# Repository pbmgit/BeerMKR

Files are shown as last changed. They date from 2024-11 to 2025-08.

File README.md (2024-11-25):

# BeerMKR
Extensions to BeerMKR machine to keep brewing if no AWS

History

I've really enjoyed brewing with the BeerMKR and I'm an Engineer (at least that's what my 40 year old degree says).
So I link to tinker and understand how and why things work.  

That applies to the beer I brew, I like to experiment.
And now that applies to the BeerMKR machine.

My BeerMKR tinkering started when I just wasn't cooling as well as I once was.  I started measuring voltages and currents on the Pelteir and decided that the heating and cooling cycles on the Peltier might have caused cracking in the solder joints which caused the resistance to rise and the current flow to fall.  With a Peltier heat transfer is proportional to current flow.
Part of that was based on this article https://www.sameskydevices.com/blog/reliability-considerations-for-peltier-modules
I also researched and changed my vibrator motor since the bushings on the original motor were so far gone that the rotor was hitting the magnets.

When I replaced the Peltier I found that I was cooling better than ever but I had some odd issues with brewing.  That got me to investigating how and when the heaters go turned on.
After that I brewed with my board connected, but clear out of my machine as I tried to figure things out.
It seems that the software on my BeerMKR board just wasn't compatible with my new Peltier.  So I started to figure out how to do the job without the BeerMKR computer.

I mapped out the connectors and ordered some of them.
I gleaned what I could from the BeerMKR board design - what parts do what.

Development

I started thinking about what I could without completely inventing the wheel.  Unrelated to my brewing I had been updating my 3D printer.  The 3D printer has temperature readings and power controls to manage the heated bed and extruder.  I thought I might use that to control the Peltier and heaters on the BeerMKR instead.
I successfully got a code change into the Marlin project that allows the heated bed power circuitry to be used to control a Peltier device (in 3D printing, when you want to cool down you just turn off whichever heater - you don't actively cool)

The BeerMKR board uses an "H-Bridge" consisting of 4 power FET transistors to turn on the Peltier in either direction.  Since the Peltier draws in excess of 8A that takes some care to replicate.
For my first pass I just used a DPDT relay configured as an H-Bridge.
For my Marlin setup I used an Arduino Mega board with a "RAMPS" (RepRap Arduino Mega Pololu Shield) to plug in on top of the Mega.  The RAMPS board has some power electronics for the heaters that we'll use and some sockets for Pololu stepper motor controls that we won't use.

For the first test the Mega was plugged into a laptop and the brewing was controlled through a serial port.  Not exactly automation, but it worked.

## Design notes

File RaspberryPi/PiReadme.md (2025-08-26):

## Current Pi settings

| | |
|:---|:---|
| Raspberry PI Imager | https://downloads.raspberrypi.org/imager/imager_latest.exe  |
| Raspberry Pi OS Lite| https://www.raspberrypi.com/software/operating-systems/ |

```
sudo apt-get update
sudo apt-get install python3-pip

sudo apt-get install python3-serial 

sudo apt install apache2 -y
sudo apt install php -y

sudo apt install python3-usb
```

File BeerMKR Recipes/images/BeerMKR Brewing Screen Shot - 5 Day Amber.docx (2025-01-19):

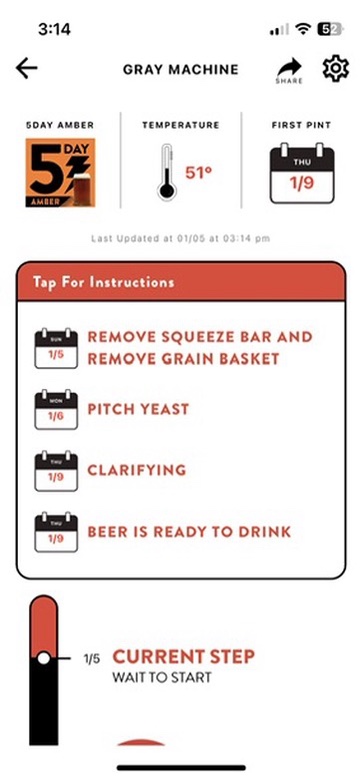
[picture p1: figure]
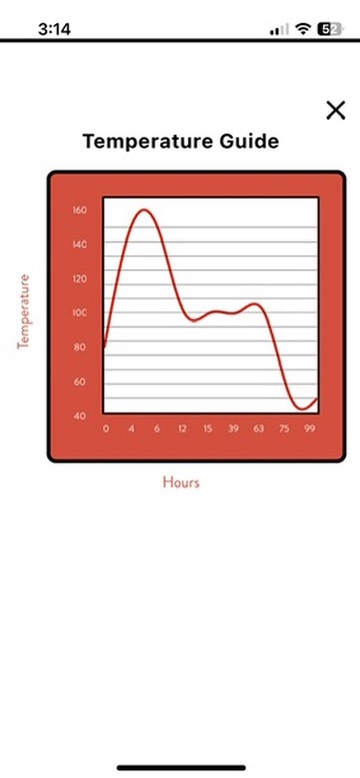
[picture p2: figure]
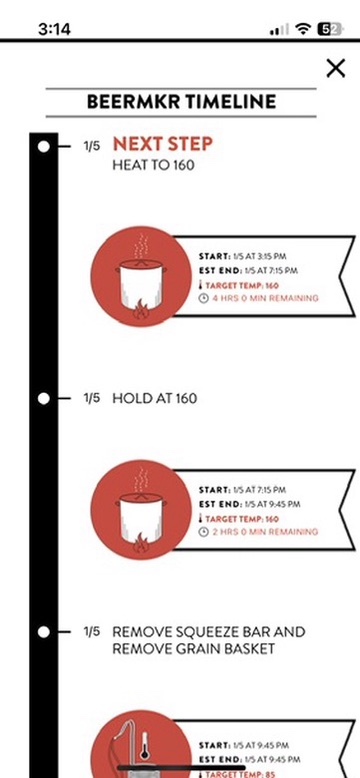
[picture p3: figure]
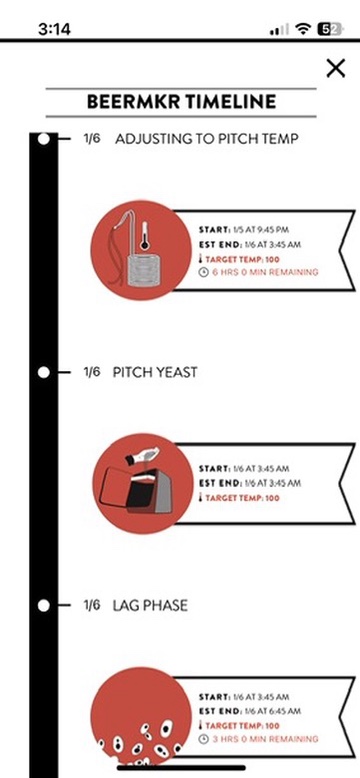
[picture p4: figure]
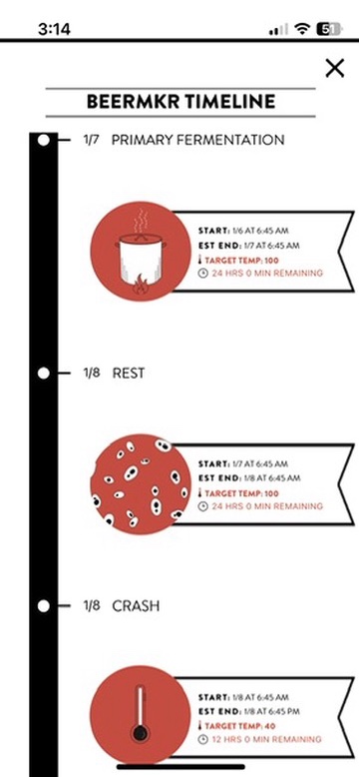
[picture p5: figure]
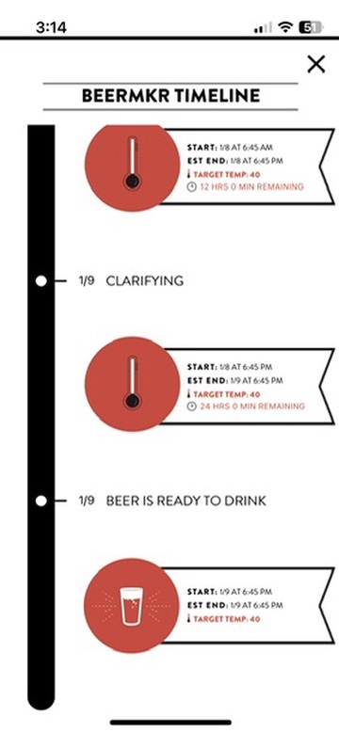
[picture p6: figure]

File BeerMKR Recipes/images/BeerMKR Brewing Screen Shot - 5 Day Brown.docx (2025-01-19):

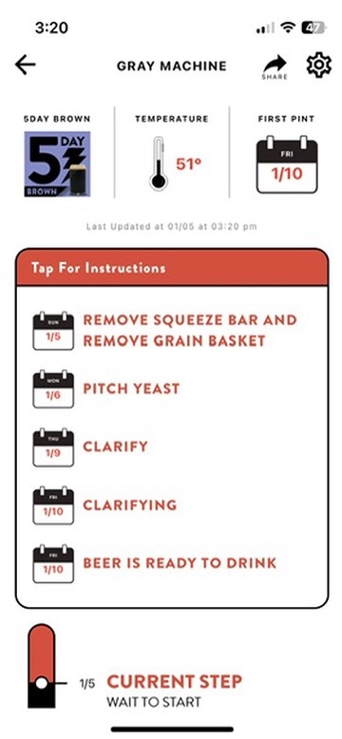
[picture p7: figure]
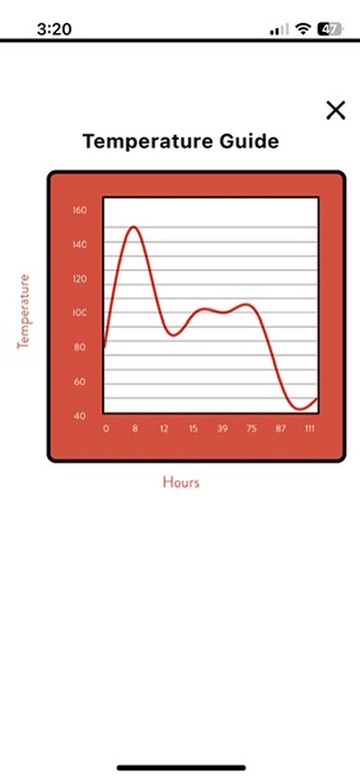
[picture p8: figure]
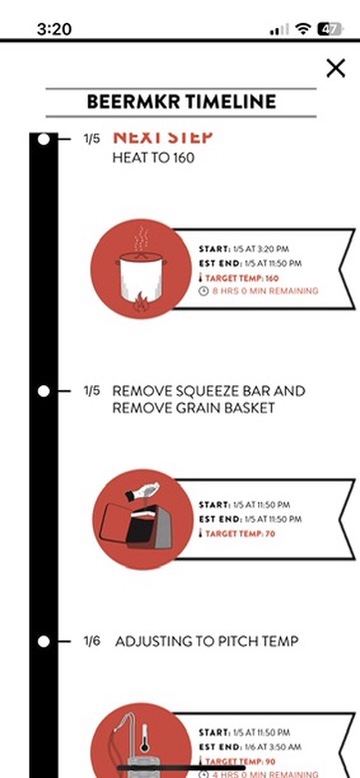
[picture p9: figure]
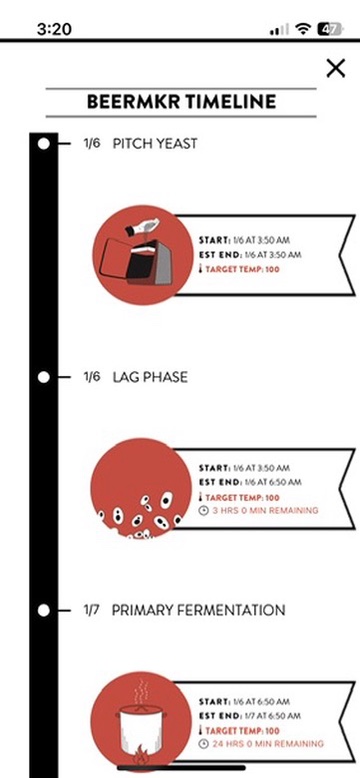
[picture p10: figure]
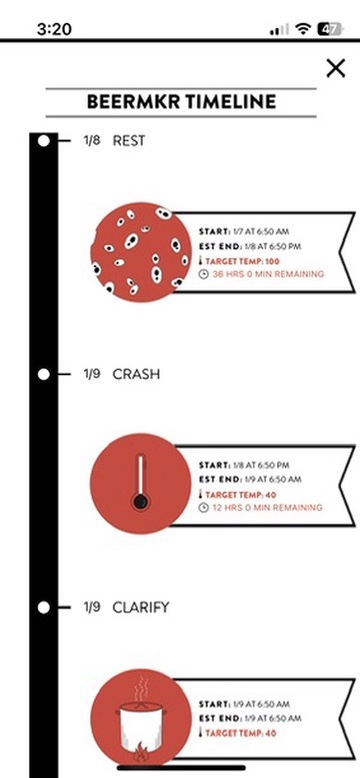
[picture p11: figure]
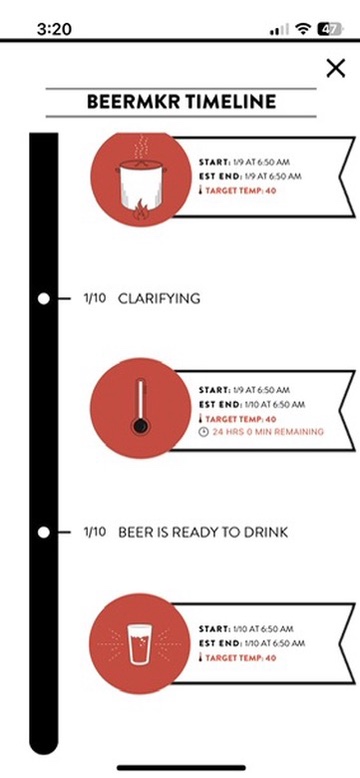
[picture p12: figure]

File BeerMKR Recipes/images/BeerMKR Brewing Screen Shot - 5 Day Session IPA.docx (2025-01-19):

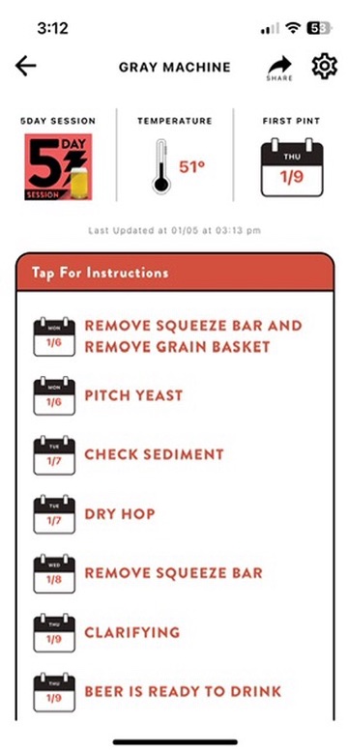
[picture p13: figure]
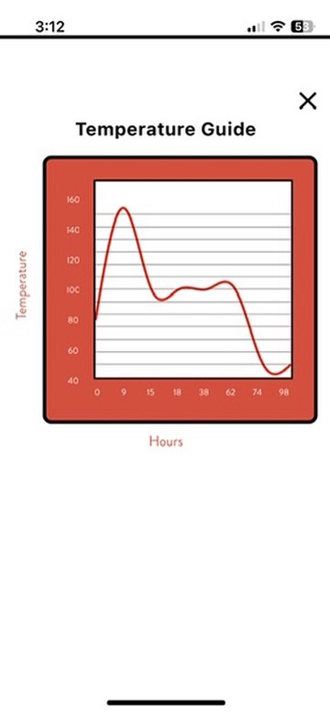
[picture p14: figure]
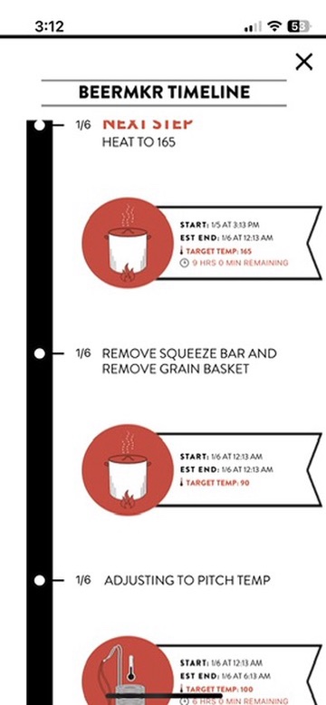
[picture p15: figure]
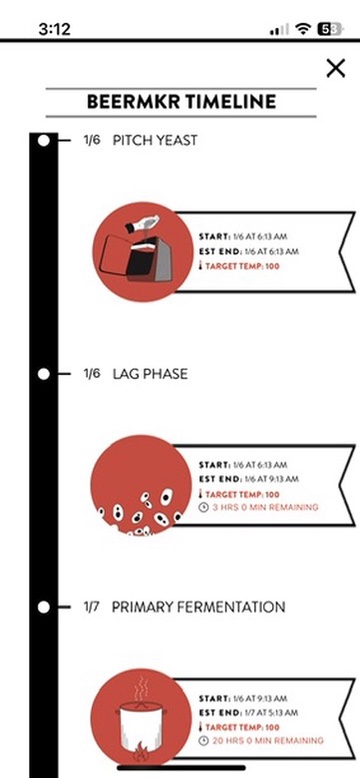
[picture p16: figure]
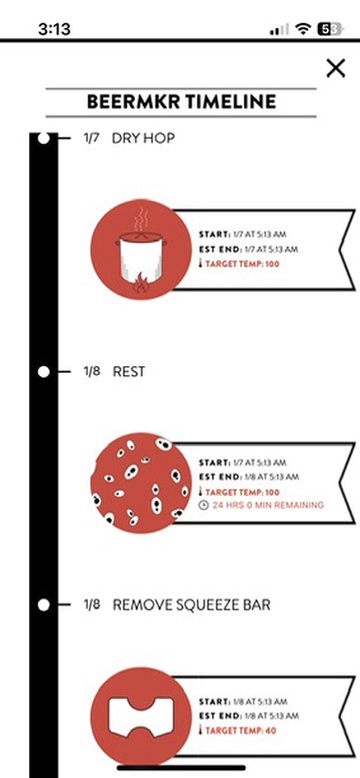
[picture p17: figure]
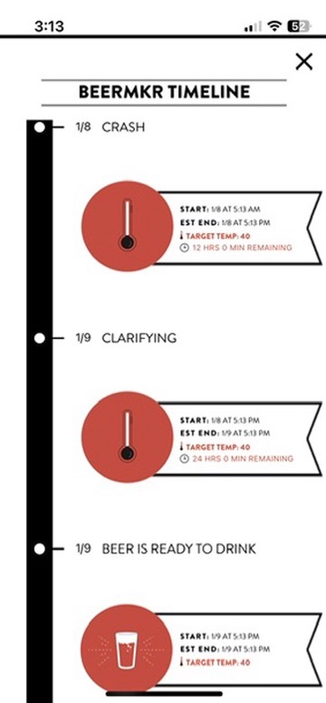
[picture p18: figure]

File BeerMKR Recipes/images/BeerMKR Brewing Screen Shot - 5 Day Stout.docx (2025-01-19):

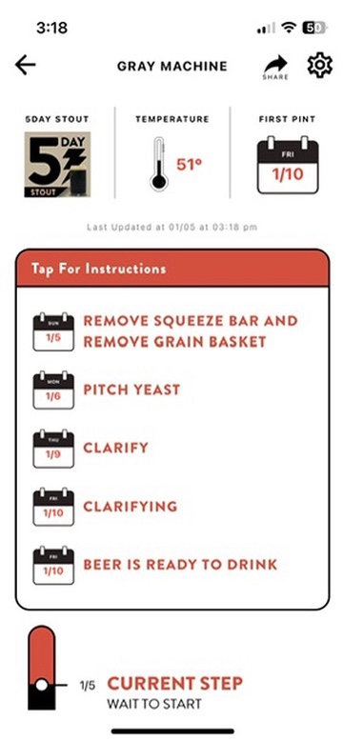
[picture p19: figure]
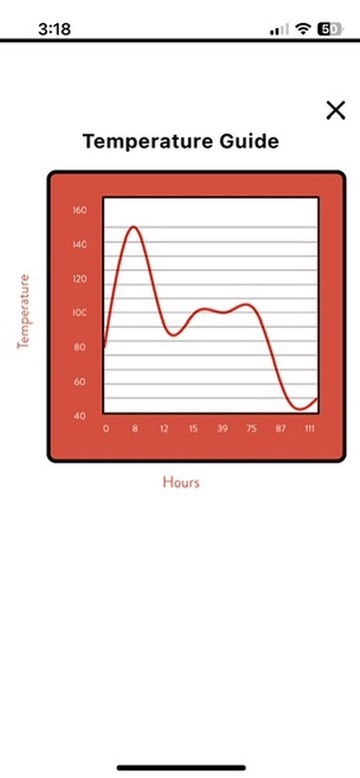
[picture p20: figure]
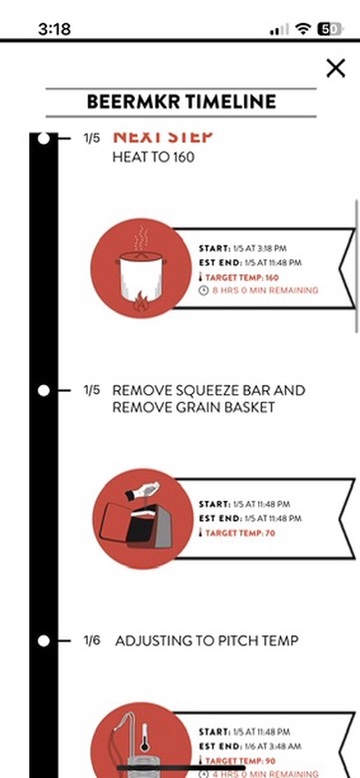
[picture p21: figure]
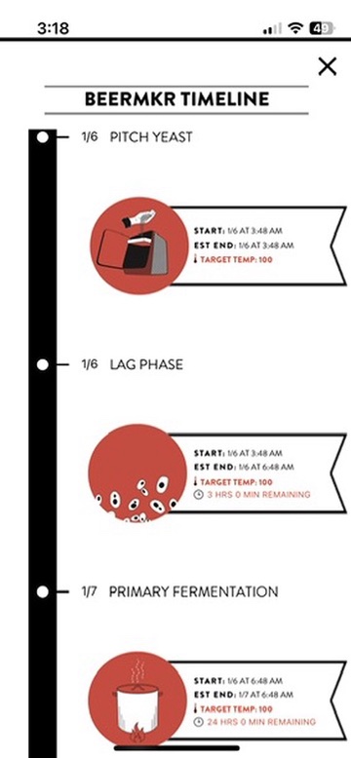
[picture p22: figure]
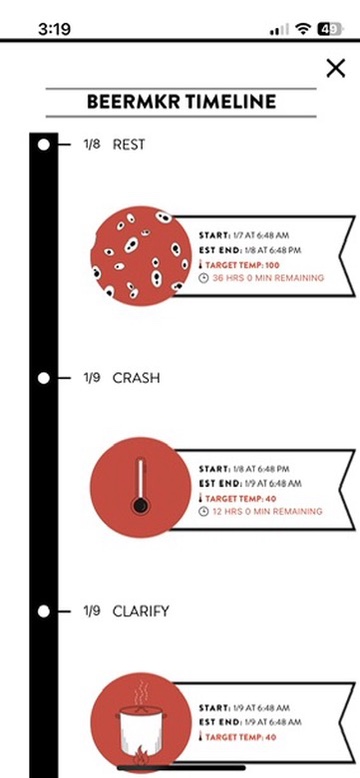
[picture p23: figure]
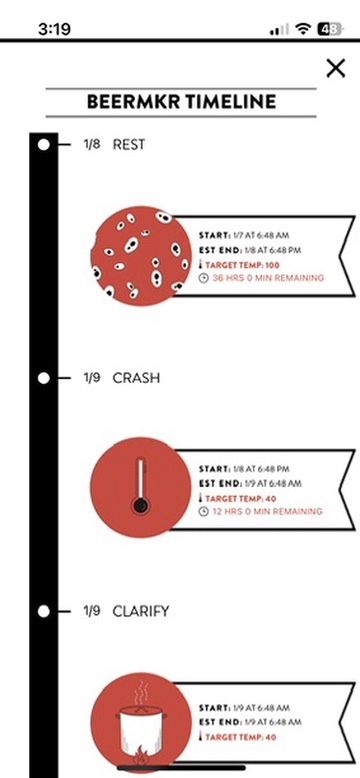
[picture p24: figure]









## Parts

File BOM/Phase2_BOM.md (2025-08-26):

Boards and Cables
- Arduino Mega 2560 board  https://www.microcenter.com/product/486545/inland-mega-2560-mainboard-arduino-compatible or Amazon
- Ramps 1.6 (Amazon or Ebay - I haven't found any place to order from where this doesn't ship from China)
- Raspberry Pi Zero 2 W + USB Power Supply
- USB OTG (On the Go) cable - Micro USB to USB-A   https://a.co/d/4iUhsvC
- Standard USB to USB-B cable (May come with Mega board) Something like this (https://a.co/d/fStud2p) that you probably already have

Parts

- MicroSD for Raspberry Pi (32G at least)

- DPDT relay 12v 10A
  - I used one of these. https://a.co/d/dN7ZP2d  The current setup drives the relay from 12.  Other setups are possible.

Peltier Connection (Rev E Boards)
- Pins	JST SVF-42T-P2.0	Digi Key 455-2347-1-ND	Qty 2	Unless you are perfect at crimping get more than 2
- Shell	JST VLR-02V	Digi Key 455-2355 ND	Qty 1	

BeerMKR Power Connector
- Pins	Hirose DF63-1618PC	Mouser 798-DF63-1618PC	Qty 2	Unless you are perfect at crimping get more than 2
- Shell	Hirose DF63A-2EP-3.96C	Mouser 798-DF63-1618PC	Qty 1	

Heater Connectors
- JST B2P-VH	Digi-Key 455-1639-ND	2 for Phase 2	I got mine in a bunch from Amazon

Temperature Sensor Connector
- JST B2B-PH-K-S	Digi-Key 455-1704-ND	Qty 1	I bought an Amazon assortment

Peltier Fan
- JST B3B-PH-K-S	Digi-Key 455-1705-ND	Qty 1

All of the rest of the connectors are JST-XH connectors. I bought this assortment: https://a.co/d/1YkNZvN

Relay Driver Electronics: TBD

- 2.5mm jack to plug in second temperature probe.  I liked these better than anything on Amazon.  I have it mounted on the left side of my BeerMKR https://www.ebay.com/itm/274570248806

The meat probe I used is gone off of Amazon.  It would be something like this: https://a.co/d/guGDll9.  Needs to be food safe.

Wire: 
- Need power wiring from BeerMKR to Printer Board, to Peltier Connector and relay assembly.  Suggest 16/2 red/black oxygen-free copper.  I used other.
- Misc 20AWG hookup wire for board jumpers and connectors
- Misc Headers

Tools
- Soldering Iron
- Wire Crimping Tool  https://a.co/d/hXJu4JY

Software (Windows)

- Visual Studio Code (for programming Marlin onto Arduino)
- Putty or other SSH terminal (for talking to Raspberry Pi)
- Raspberry Pi loader

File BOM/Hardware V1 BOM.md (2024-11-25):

Bill of Materials for Version 1
(Amazon references aren't what I used, just a convenient reference)

Boards
Arduino Mega 2560 or clone (Mine came from Microcenter for $20)
https://www.amazon.com/ELEGOO-Compatible-Arduino-Projects-Compliant/dp/B01H4ZLZLQ

RAMPS 1.6 board (the 1.6 has better power electronics arrangements)
https://www.amazon.com/SIUKE-Heatsink-Expansion-Mainboard-Accessories/dp/B0CS6PJ69F

Connectors

Peltier - JST VL (Digi-Key)
Shell VLR-02V  (Digi-Key 455-2355-ND)
Pins SVF-42T-P2.0  (Digi Key 455-2347-1-ND)

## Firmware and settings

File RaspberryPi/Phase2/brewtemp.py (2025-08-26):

#!/usr/bin/python3
import serial
import os
import datetime
import time

def logger(logstate, logstring):
  if not logstate:
    return

  with open('marlinlog.log','a') as log:
    lognow=datetime.datetime.now().strftime("%Y-%m-%d %H:%M:%S")
    logstringdt = lognow + " " + logstring + "\n"
    log.write(logstringdt)

def check_marlin_queue(logstate, rf=True):
  """
  Process commands from marlinqueue.cmd file
  :param logstate: current logging state (True/False)
  :param rf: loop control flag (default True)
  :returns: tuple (logstate, rf) - logging state and loop control
  """
  with open('marlinqueue.cmd','r+') as cmdfile:
    while rf:
      serwrite = True
      cmdline = cmdfile.readline()
      #print('[' + cmdline + ']')
      if cmdline.lower().startswith('logging:on'):
        logstate = True
        serwrite = False
      if cmdline.lower().startswith('logging:off'):
        logger(logstate, cmdline)
        logstate = False
        serwrite = False

      if cmdline.startswith('#'):
        global brewstate
        brewstate = cmdline
        serwrite = False

      if cmdline.startswith('ABORT'):
        cmdfile.truncate(0)
        logger(logstate, cmdline)
        exit()
      if len(cmdline) == 0:
        cmdfile.truncate(0)
        rf = False
        return logstate, rf

      logger(logstate, cmdline)

      if serwrite:
        ser.write(cmdline.encode())

    return logstate, rf

def check_reply(logstate, mreply):
  """
  Process replies from Marlin firmware
  :param logstate: current logging state (True/False)
  """
  while mreply:
    line = ser.readline()
    if len(line) == 0:
      break
    ooo = line.decode()
    logger(logstate, ooo)

    if ooo.startswith(' T:'):
      lognow=datetime.datetime.now().strftime("%Y-%m-%d %H:%M:%S")
      with open('statusfile','w') as stfile:
        stfile.write(lognow + '\n')
        stfile.write(brewstate)
        stfile.write(ooo)

# Initialize variables
ooo = "Beginning Text"
# To be able to test
logstate = False
mreply = True
brewstate = "brewtemp initialization\n"

ser = serial.Serial(port='/dev/ttyACM0', baudrate=250000, parity=serial.PARITY_NONE, timeout=1)
ser.isOpen()

run = True
# Main Loop only runs when file is executed directly
if __name__ == '__main__':
  while run:
    # Input Command Section
    # Read batch of commands from input file then truncate
    logstate, rf = check_marlin_queue(logstate, True)

    # Marlin reply Section
    check_reply(logstate, mreply)

    time.sleep(5)

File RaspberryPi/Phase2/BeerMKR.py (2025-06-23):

#!/usr/bin/python3

import datetime
import time
from datetime import timedelta 

#Delay variables
tempwait = False
timewait = False
buttonwait = False

bagTempWaitValue = 40 
grainTempWaitValue = 0
waitDT = datetime.datetime.now()


filepath = '/home/BeerPi'
recipefile ='recipe.bmkr'
logfilename = 'brewlog.log'
recipestatefile = 'reciperunningstate'
marlinqueue = 'marlinqueue.cmd'
statusfile = 'statusfile'

def logger(logstate, logstring):

   if not logstate:
      return

   with open(logfilename,'a') as log:
      lognow=datetime.datetime.now().strftime("%Y-%m-%d %H:%M:%S")
      logstringdt = lognow + " " + logstring + "\n"
      log.write(logstringdt)


def marlincmd(cmdstring):
   try: 
        with open('marlinqueue.cmd','a') as cmdfile:
            cmdfile.write(cmdstring + "\n")
            print ('--->' + cmdstring + "\n")
   except Exception as e:
        print(f"An error occurred: {e}")

def checkdelay():
#  this is a blocking module.  Execution will not exit this module until block conditions are passed
   
   checktempdelay()
   checktimedelay()
   checkbutton(buttonwait)

# temperature checking.  This returns when temperature conditions have been met
def  checktempdelay():
   global tempwait
   global bagTempWaitValue
   global grainTempWaitValue
   while tempwait:
      with open(statusfile,'r') as sf:
         timetag = sf.readline()
         statelabel = sf.readline()
         tempstate = sf.readline()
         fields = tempstate.split(' ')
         print(fields)
         tokens = fields[1].split(':')
         graintemp = int(float(tokens[1]))
         tokens = fields[3].split(':')
         bagtemp = int(float(tokens[1]))
         print('In temperature wait loop')
         print(graintemp)
         print(bagtemp)
         if bagTempWaitValue != 0 and bagtemp == bagTempWaitValue:
            tempwait = False
            bagTempWaitValue = 0

         elif grainTempWaitValue != 0 and graintemp == grainTempWaitValue:
            tempwait = False
            grainTempWaitValue = 0
            
        

         loopwait = 15
         time.sleep(loopwait)


def checktimedelay():
    global timewait
    global waitDT
    
    while timewait:
        print('In Time Wait Loop.  Target ' + waitDT.ctime())
        if datetime.datetime.now() > waitDT:
            timewait = False
            
        loopwait = 15
        time.sleep(loopwait)
    
    
def checkbutton():
    global buttonwait
    if buttonwait:
        while buttonwait:
            print('In Button Wait')
            with open('buttonfile','r+') as btfile:
                ptext = btfile.readline()
                print('Bstatus... [' + ptext + ']')
                if ptext.strip().lower() == 'pressed':
                    print('Button Press Detected')
                    buttonwait = False
                    btfile.truncate(0)
                    break
        
            loopwait = 15
            time.sleep(loopwait)

            
    
         




defaultmonitorinterval = 60

recipe = []
rindex = 0

with open(recipefile) as rf:
   for lines in rf:
      recipe.append(lines.strip())


print(recipe)

stepnum = 0

for step in recipe:
    
#check for programmed delays
   checktempdelay()
   checktimedelay()
   checkbutton()
   print('After Delay Checks')

# Parse recipe step
   print(step)
   nugget = step.split(':')
   print(nugget)
   print(nugget[0].lower())

# Steps that require no token parsing
   if step == 'logging:on' or step == 'logging:off':
        marlincmd(step)
        
   elif step.startswith('#'):
        marlincmd(step)
     
# Steps that require examining tokens (nugget variable)
   elif nugget[0].lower() == 'monitor':
# Monitor:Off code
        if nugget[1] == 'off':
            marlincmd('M155 S0')
        elif nugget[1] == 'on':
# Monitor on with optional interval setting
            interval = defaultmonitorinterval
            if len(nugget) > 2:
                interval = int(nugget[2])
       
            marlincmd('M155 S' + str(interval))

# Bag Temperature Set Section
   elif nugget[0].lower() == 'bag':
        if nugget[1].lower() == 'off':
            marlincmd('M140 S0')
        elif nugget[1].lower() == 'set':
            tempC = int(nugget[2])
            marlincmd('M140 S' + str(tempC))
            
            if len(nugget) > 3:
                print("Bag hold temperature detected")
                if nugget[3].lower() == 'wait':
                    tempwait = True
                    bagTempWaitValue = tempC
            

# Grain Temperature Set Section
   elif nugget[0].lower() == 'grain':
        if nugget[1].lower() == 'off':
            marlincmd('M104 S0')
        elif nugget[1].lower() == 'set':

            tempC = int(nugget[2])
            
            marlincmd('M104 S' + str(tempC))
            print("Nugget Length " + str(len(nugget)))
            if len(nugget) > 3:
                if nugget[3].lower() == 'wait':
                    print('Grain hold temperature detected')
                    tempwait = True
                    grainTempWaitValue = tempC

# Wait section
   elif nugget[0].lower() == 'wait':
        print('Wait Parsing')
 
#  Button Wait parsing
        if nugget[1].lower() == 'button':
            print('Button Wait Parsing')
            buttonwait = True
            

# Wait (time) section
        else:
            print('Time Wait Parsing')
            secsdelay = int(nugget[1])
            interval = timedelta(seconds=secsdelay)
            waitDT = datetime.datetime.now() + interval
            timewait = True

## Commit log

2024-11-25 Create Hardware V1 BOM
2025-01-16 Create PiReadme
    Initial Raspberry Pi software and configuration
2025-01-16 Create Phase2_BOM
    Initial Bill of Materials for a Phase 2 BeerMKR controller
2025-06-20 Add files via upload
    Incomplete Phase 2 schematic. This schematic should cover relay driver, temperature inputs, power connections, heater connections (power drive for heaters and Peltier are off board on the RAMPS board)
    [Phase2Drive.kicad_sch]
2025-06-23 Create brewtemp.py
    Phase 2 interface to 3D printer board. Command transfers and temperature reporting.
2025-06-23 Create dopplebock.bmkr
    Sample recipe for phase 2 BeerMKR.py interpretation
2025-08-22 Added Unit tests Created markdown files for the BOMs in the BOM folder Refactored the code to make testing it easier
